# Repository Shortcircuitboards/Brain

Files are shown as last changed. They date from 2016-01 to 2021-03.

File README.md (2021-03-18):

# -//Brain
OSD PCB wit Sensors and usefull stuff for the FPV Rover

The Rover-Brain is complete PDB with integratetd OSD, BEC, Current Sensor, Voltage Sensor, RSSI Filter, LC Filter, and 3 Step Switch. 
It´s to keep the FPV-Rover Clean of a wire mess and to have all necessary information of your onboard system in your Video-Downlink.

I used a Mashup of the Legendary E-OSD and put some sensors and other usefull parts on one PCB. It fit´s for 2S and 3S.

The Development, Schematic and Software of the 3-Way Switch was done by JReise http://jreise.de/ (more software and Infos)
The Development, Schematic and Software of the E-OSD was done by ?? Arrgh i dont know ^^

For Setting it up You just need an USBASP to flash the OSD Firmware and the .HEX file of the AtTiny13 which is in use as an 3-Step Swicht (for flashing the pure .hex file i Use Burn-O-Mat) 
Here is the software for the attiny13: http://jreise.de/RCUSB/Daten/2-Stufen-RC-Schalter.zip  all rights by JReise !!!  Since his page is just accessible over waybackmachine.com i Uploaded the neccessary hex file to flash the attiny13

For the OSD i use the G-OSD GUI which is awseome and easy to handel !

You can manually set up the Voltage Divider with the Potentiometer P1 and the output of the Currentsensor with P2, so you can easyily adjust it to exactly that value that you need.

Pinout Legend (will be countinued later):
1 = ESC1 PWM
2 =
3 = 
4 = 
5 =
6 =
7 =
8 =
9 =
10=
11=
12=
13=
14=
15=
16=
17=
18= ESC2 PWM

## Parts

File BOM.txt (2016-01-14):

Partlist

Exported from Brain_V0_1.brd at 12.01.2016 13:22:20

EAGLE Version 6.3.0 Copyright (c) 1988-2012 CadSoft

Assembly variant: 

Part            Value            Package            Library                Position (mm)         Orientation

AKKU1           XT-60            XT-60              RoboJackets-Connectors (29.845 75.565)       R90
AKKU2           XT-60            XT-60              RoboJackets-Connectors (29.845 29.845)       R90
C1              1nF              C0603K             resistor               (42.545 38.1)         R0
C2              0,1uF            C0603K             resistor               (48.26 43.18)         R0
C3              0,1uF            C0603K             resistor               (39.37 53.975)        R0
C4              22pF             C0603K             rcl                    (36.83 36.195)        R180
C5              22pF             C0603K             rcl                    (48.26 38.1)          R0
C6              100nF            C0603K             rcl                    (62.23 52.07)         R0
C7              100nF            C0603K             rcl                    (36.83 33.02)         R0
C8              100nF            C0603K             rcl                    (55.88 36.83)         R180
C9              220pF            C0603K             rcl                    (52.07 30.48)         R180
C10             470nF            C1206              rcl                    (55.88 54.61)         R0
C11             470nF            C1206              rcl                    (55.88 50.8)          R0
C12             220pF            C0603K             rcl                    (59.69 31.75)         R90
C13             100nF            C0603K             rcl                    (60.96 43.18)         R0
C14             330uF            153CLV-0807        rcl                    (58.42 74.93)         R180
C15             100nF            C0603K             rcl                    (52.07 33.02)         R180
D1              1N4448W          SOD523             diode                  (38.1 40.64)          R0
D2                               DO-214AC           diode                  (57.15 59.69)         R180
IC1             MEGA8-AI         TQFP32-08          atmel                  (40.64 60.96)         R0
IC2             TINY13-20SSU     8S1                atmel                  (39.37 27.94)         R90
L1              330uH            POWER-CHOKE_WE-TPC rcl                    (48.26 76.2)          R90
LADEN           XT-60            XT-60              RoboJackets-Connectors (3.175 49.53)         R0
LED1                             CHIP-LED0603       led                    (43.18 76.2)          R0
Q1              CSM-7X-DU        CSM-7X-DU          crystal 16 mhz               (26.035 37.465)       R180
Q2              BC807-40SMD      SOT23-BEC          transistor-pnp         (62.23 66.04)         R0
R1              2K               R0603              resistor               (39.37 51.435)        R0
R2              R Errechnen !    R0603              resistor               (45.72 53.975)        R0
R3              1K               R0603              rcl                    (33.655 43.815)       R0
R4              15K              R0603              rcl                    (62.23 60.96)         R0
R5              3K               R0603              rcl                    (33.655 41.275)       R0
R6              1K               RTRIM3103          rcl                    (21.59 43.18)         R0
R7              15K              R0603              rcl                    (42.545 34.925)       R180
R8              1K               RTRIM3103          rcl                    (27.94 43.18)         R0
R9              3K               R0603              rcl                    (55.88 46.99)         R0
R10             5K6              R0603              rcl                    (55.88 39.37)         R0
R11             1k               R0603              rcl                    (60.96 40.64)         R180
R12             120R             R0603              rcl                    (62.23 54.61)         R0
R13             180R             R0603              rcl                    (62.23 49.53)         R0
R14             1K2              R0603              rcl                    (55.88 33.02)         R0
R15             1k               R0603              rcl                    (43.18 71.12)         R270
R16             1k5              R0603              rcl                    (55.88 29.21)         R0
R17             100k             R0603              rcl                    (62.23 46.99)         R0
R18             100k             R0603              rcl                    (55.88 43.18)         R0
SW_1            PTR2             P2-38-17           testpad                (3.175 68.58)         R180
T1              SMD300F          SMD050F            switch-raychem         (36.83 74.93)         R0
U$1             REED-RELAIS      REED-RELAIS        				       (70.485 53.975)       R90
U$2             IRLM2502         SOT23              				       (45.72 27.94)         R0
U$3             I_SENSE_IC       SOIC8              				       (12.7 41.275)         R270
U$4             ICSP_6P          ICSP_6P            				       (43.815 48.895)       R180
U$5             IRLM2502         SOT23              				       (49.53 27.94)         R0
VIDEO_OUT       OSD einschleifen JP1                jumper                 (55.88 64.77)         R0

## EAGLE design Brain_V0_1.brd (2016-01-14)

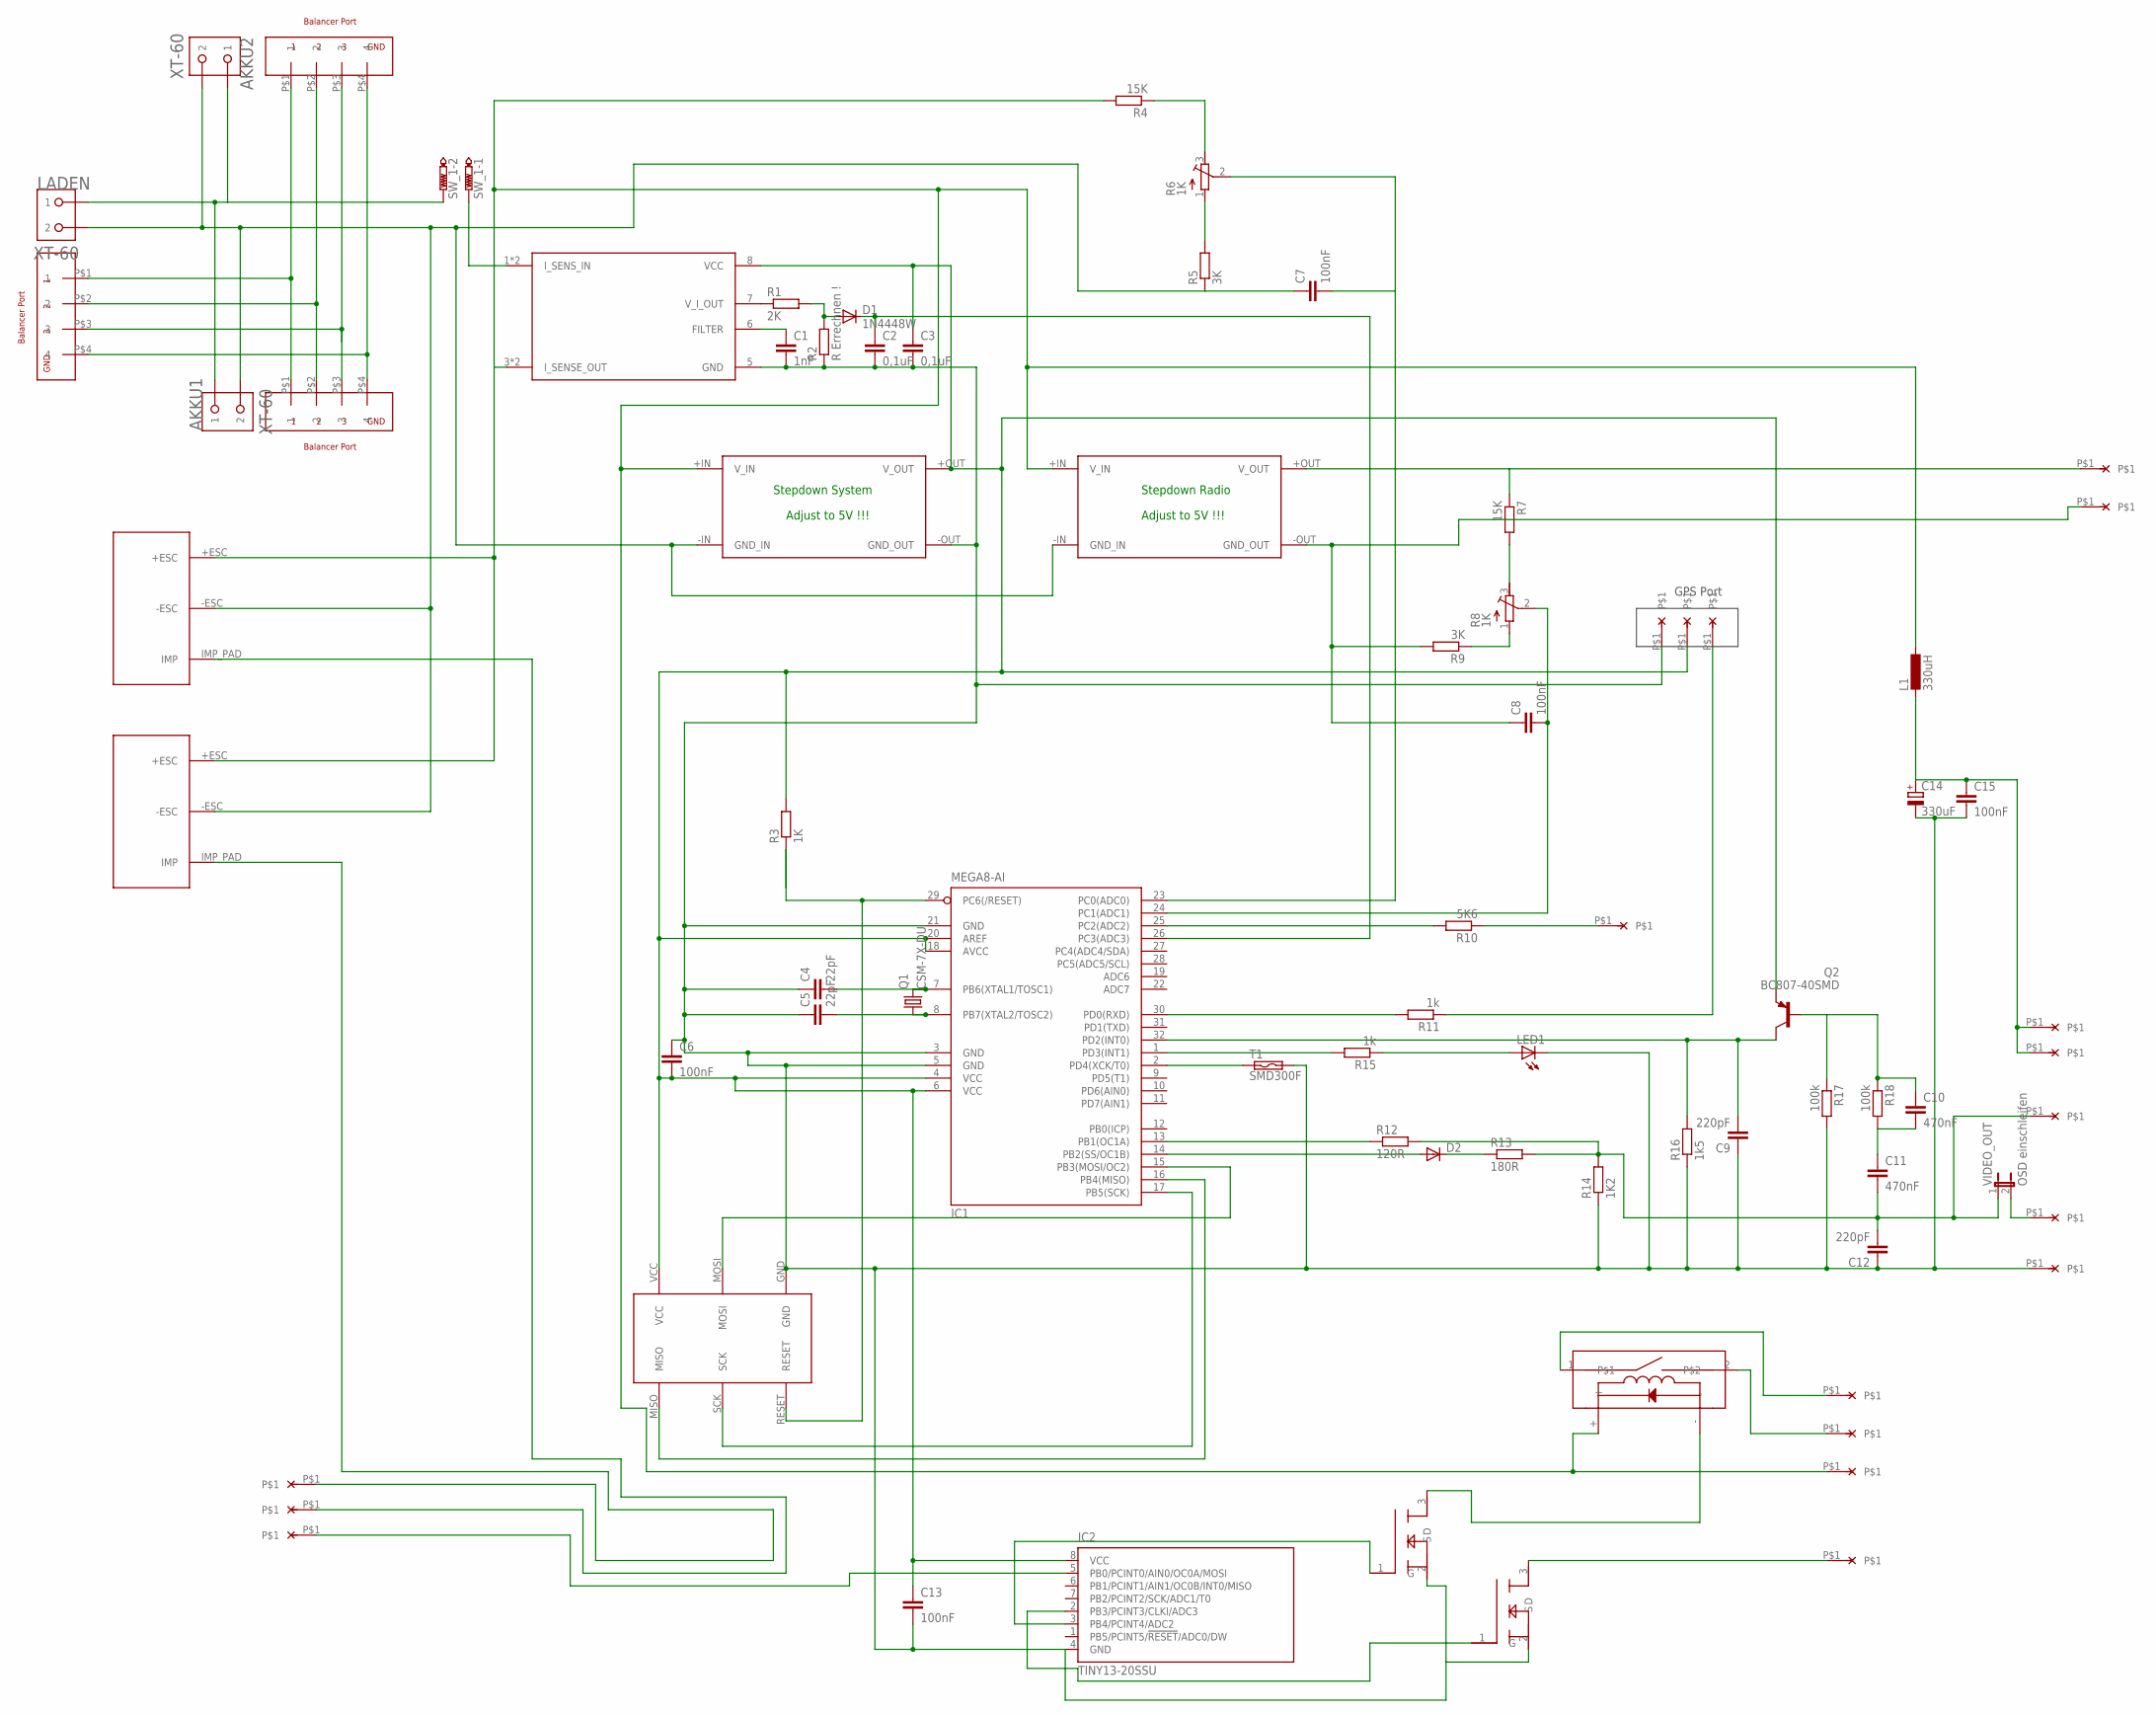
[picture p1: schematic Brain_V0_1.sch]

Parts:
5V_GPS: LöTPAD_KLEIN
AKKU1, AKKU2: XT-60
BALANCER_1, BALANCER_2: BALANCER_3S
BALANCE_OUT: BALANCER_3S
BEC+: LöTPAD_KLEIN
BEC-: LöTPAD_KLEIN
C1: 1nF; C0603K
C2, C3: 0,1uF; C0603K
C4, C5: 22pF; C0603K
C6, C7, C8, C13, C15: 100nF; C0603K
C9, C12: 220pF; C0603K
C10, C11: 470nF; C1206
C14: 330uF; 153CLV-0807
CAMERA_VIDEO: LöTPAD_KLEIN
CH1_IN, CH2_IN, CH3_IN: LöTPAD_KLEIN
D1: 1N4448W; SOD523
D2: DIODE-DO-214AC; DO-214AC
ESC1, ESC2: MOT_CONNECTOR
FILTER: LöTPAD_KLEIN
FILTER_: LöTPAD_KLEIN
GND_GPS: LöTPAD_KLEIN
GND_VIDEO: LöTPAD_KLEIN
IC1: MEGA8-AI; TQFP32-08
IC2: TINY13-20SSU; 8S1
IR_GND: LöTPAD_KLEIN
IR_VCC: LöTPAD_KLEIN
L1: 330uH; POWER-CHOKE_WE-TPC
LADEN: XT-60
LED1: LEDCHIP-LED0603; CHIP-LED0603
Q1: CSM-7X-DU
Q2: BC807-40SMD; SOT23-BEC
R1: 2K; R0603
R2: R Errechnen !; R0603
R3: 1K; R0603
R4, R7: 15K; R0603
R5, R9: 3K; R0603
R6, R8: 1K; RTRIM3103
R10: 5K6; R0603
R11, R15: 1k; R0603
R12: 120R; R0603
R13: 180R; R0603
R14: 1K2; R0603
R16: 1k5; R0603
R17, R18: 100k; R0603
RSSI_IN: LöTPAD_KLEIN
RX_GPS: LöTPAD_KLEIN
STEPDOWN_RADIO: STEPDOWN_MINI; STEPDOWN_SMALL
STEPDOWN_SYSTEM: STEPDOWN_MINI; STEPDOWN_SMALL
SW_1: PTR2; P2-38-17
T1: SMD300F; SMD050F
U$1: REED-RELAIS
U$2, U$5: IRLM2502; SOT23
U$3: I_SENSE_IC; SOIC8
U$4: ICSP_6P
VCC_CAM: LöTPAD_KLEIN
VCC_VTX: LöTPAD_KLEIN
VIDEO: LöTPAD_KLEIN
VIDEO_OUT: OSD einschleifen; JP1

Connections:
unnamed: AKKU1.BATT (1), AKKU2.BATT (1), LADEN.BATT (1), SW_1.TP-2
unnamed: AKKU1.GND (2), AKKU2.GND (2), C7.1, ESC1.-ESC, ESC2.-ESC, LADEN.GND (2), R5.1, STEPDOWN_RADIO.-IN (GND_IN), STEPDOWN_SYSTEM.-IN (GND_IN)
unnamed: BALANCER_1.P$1 (1), BALANCER_2.P$1 (1), BALANCE_OUT.P$1 (1)
unnamed: BALANCER_1.P$2 (2), BALANCER_2.P$2 (2), BALANCE_OUT.P$2 (2)
unnamed: BALANCER_1.P$4 (4), BALANCER_2.P$4 (4), BALANCE_OUT.P$4 (4)
unnamed: SW_1.TP-1, U$3.1 (I_SENS_IN), U$3.2 (I_SENS_IN)
unnamed: 5V_GPS.P$1, C3.1, C6.2, C13.1, IC1.4 (VCC), IC1.6 (VCC), IC1.18 (AVCC), IC1.20 (AREF), IC2.8 (VCC), Q2.E, R3.2, STEPDOWN_SYSTEM.+OUT (V_OUT), U$3.8 (VCC), U$4.VCC
unnamed: C4.2, IC1.7 (PB6(XTAL1/TOSC1)), Q1.2
unnamed: C1.1, U$3.6 (FILTER)
unnamed: R1.1, U$3.7 (V_I_OUT)
unnamed: D1.A, R1.2, R2.2
unnamed: C2.1, D1.C, IC1.26 (PC3(ADC3))
unnamed: FILTER_.P$1, U$1.2
unnamed: C5.2, IC1.8 (PB7(XTAL2/TOSC2)), Q1.1
unnamed: IC1.29 (PC6(/RESET)), R3.1, U$4.RESET
unnamed: IC1.15 (PB3(MOSI/OC2)), U$4.MOSI
unnamed: IC1.17 (PB5(SCK)), U$4.SCK
unnamed: R4.1, R6.3 (E)
unnamed: IC1.16 (PB4(MISO)), U$4.MISO
unnamed: R5.2, R6.1 (A)
unnamed: VIDEO.P$1, VIDEO_OUT.2
unnamed: C7.2, IC1.23 (PC0(ADC0)), R6.2 (S)
unnamed: R7.2, R8.3 (E)
unnamed: R8.1 (A), R9.1
unnamed: BEC-.P$1, C8.1, R9.2, STEPDOWN_RADIO.-OUT (GND_OUT)
unnamed: C8.2, IC1.24 (PC1(ADC1)), R8.2 (S)
unnamed: IC1.25 (PC2(ADC2)), R10.2
unnamed: R10.1, RSSI_IN.P$1
unnamed: IC1.30 (PD0(RXD)), R11.2
unnamed: R11.1, RX_GPS.P$1
unnamed: IC1.2 (PD4(XCK/T0)), T1.1
unnamed: IC1.13 (PB1(OC1A)), R12.1
unnamed: C11.2, C12.2, CAMERA_VIDEO.P$1, R12.2, R13.2, R14.2, VIDEO_OUT.1
unnamed: D2.A, IC1.14 (PB2(SS/OC1B))
unnamed: D2.C, R13.1
unnamed: IC1.1 (PD3(INT1)), R15.2
unnamed: LED1.A, R15.1
unnamed: CH1_IN.P$1, ESC2.IMP_PAD (IMP)
unnamed: CH2_IN.P$1, ESC1.IMP_PAD (IMP)
unnamed: CH3_IN.P$1, IC2.5 (PB0/PCINT0/AIN0/OC0A/MOSI)
unnamed: FILTER.P$1, U$1.1
unnamed: ESC1.+ESC, ESC2.+ESC, IR_VCC.P$1, L1.1, R4.2, STEPDOWN_RADIO.+IN (V_IN), STEPDOWN_SYSTEM.+IN (V_IN), U$1.+, U$3.3 (I_SENSE_OUT), U$3.4 (I_SENSE_OUT)
unnamed: C9.2, IC1.32 (PD2(INT0)), Q2.C, R16.2
unnamed: C10.1, Q2.B, R17.1, R18.1
unnamed: BALANCER_1.P$3 (3), BALANCER_2.P$3 (3), BALANCE_OUT.P$3 (3)
unnamed: C10.2, C11.1, R18.2
unnamed: IC2.3 (PB4/PCINT4/ADC2), U$2.1 (G)
unnamed: IC2.2 (PB3/PCINT3/CLKI/ADC3), U$5.1 (G)
unnamed: U$1.-, U$2.3 (D)
unnamed: IR_GND.P$1, U$5.3 (D)
unnamed: BEC+.P$1, R7.1, STEPDOWN_RADIO.+OUT (V_OUT)
unnamed: C14.+, C15.1, L1.2, VCC_CAM.P$1, VCC_VTX.P$1
unnamed: C1.2, C2.2, C3.2, C4.1, C5.1, C6.1, C9.1, C12.1, C13.2, C14.-, C15.2, GND_GPS.P$1, GND_VIDEO.P$1, IC1.3 (GND), IC1.5 (GND), IC1.21 (GND), IC2.4 (GND), LED1.C, R2.1, R14.1, R16.1, R17.2, STEPDOWN_SYSTEM.-OUT (GND_OUT), T1.2, U$2.2 (S), U$3.5 (GND), U$4.GND, U$5.2 (S)

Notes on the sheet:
Stepdown System
Stepdown Radio
Adjust to 5V !!!
GPS Port

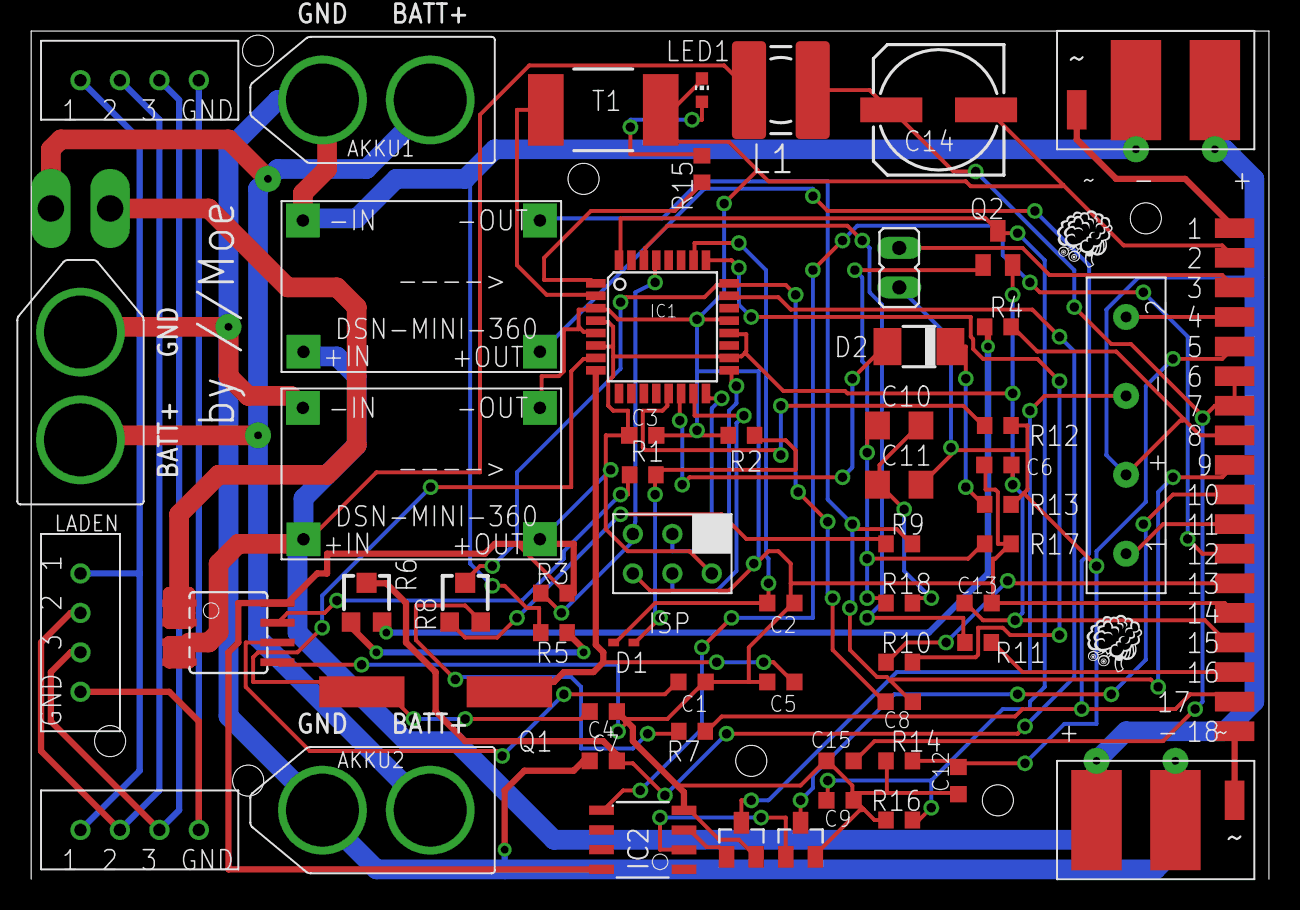
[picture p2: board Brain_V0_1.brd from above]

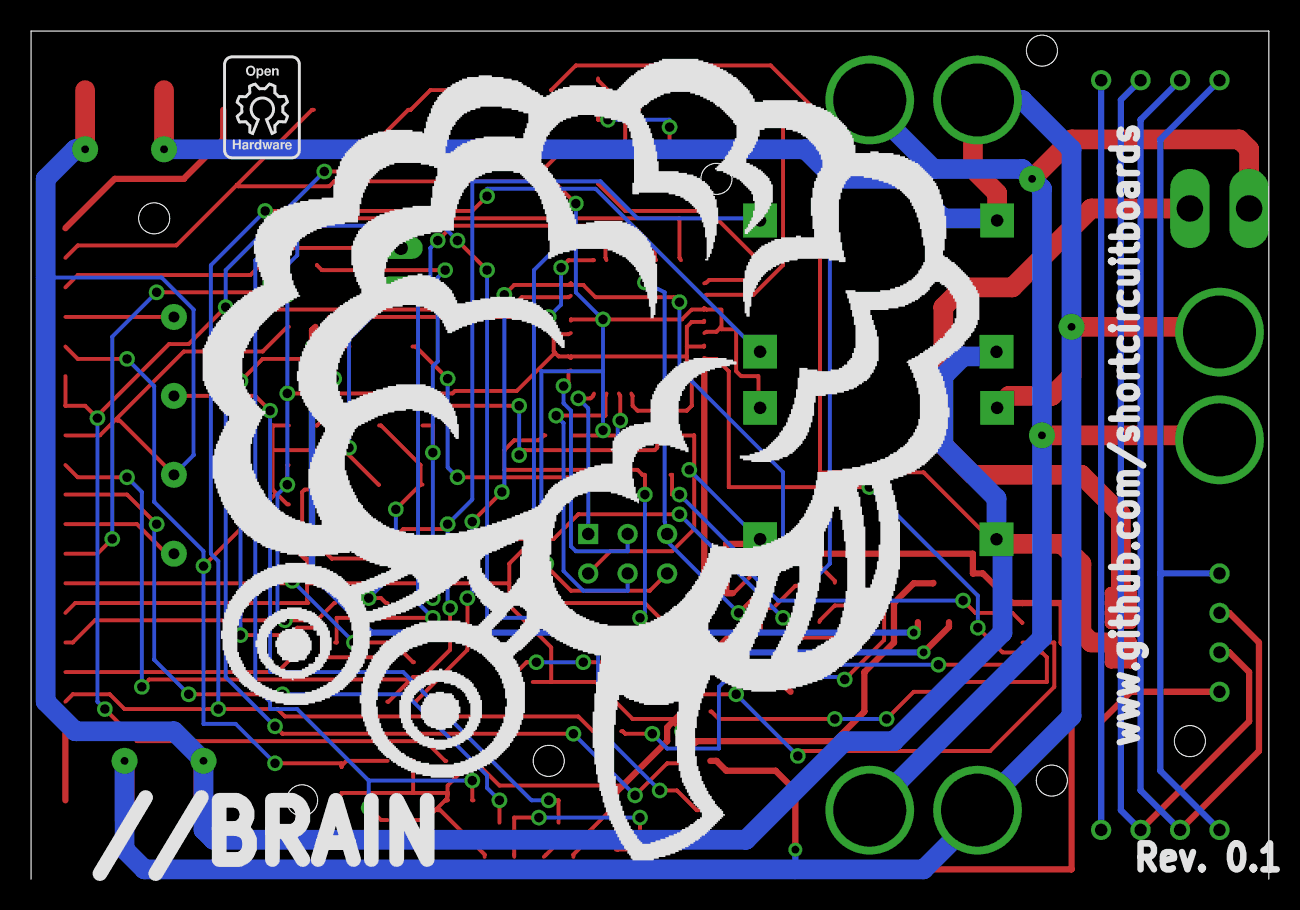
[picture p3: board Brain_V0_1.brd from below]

Board: 2 copper layers, 79.7 x 54.6 mm, 81 parts (2 on the bottom side), 53 nets.

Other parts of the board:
E$1, E$2: BRAINLOGO
E$3: BRAINLOGO_BIG
E$4: OPEN_HARDWARE_SMALL
